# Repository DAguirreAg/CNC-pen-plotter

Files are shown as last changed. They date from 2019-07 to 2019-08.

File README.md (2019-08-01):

# CNC-pen-plotter
A multi axes (XY) CNC pen plotter machine.

<p align="middle">
  Drawing with the CNC machine

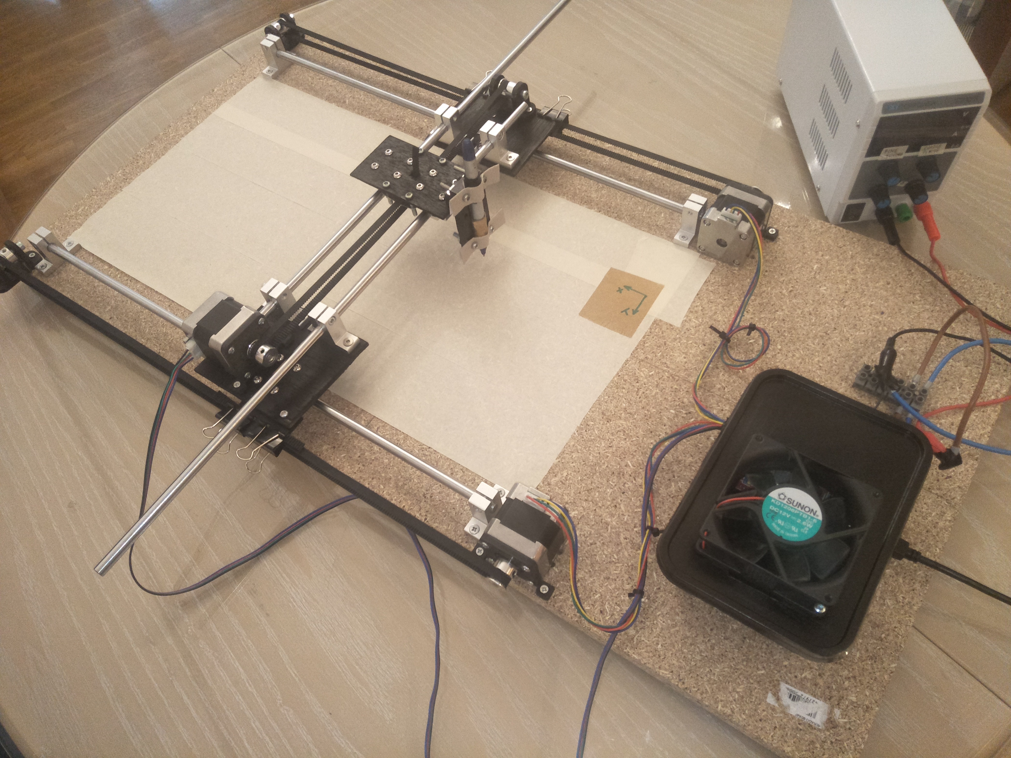
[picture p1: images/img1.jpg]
Complete view of the CNC assembly
  
</p>

## 1. Introduction
The following repository holds the code, schematics and hardware needed to build a simple two linear axes plotter controlled with an Arduino and a CNC shield. 

The X axis is controlled by **two Nema 17 stepper motors** and the Y axis is controlled by **another Nema 17 stepper motor**.

The commands are sent via the “Universal GCode sender” and the GCode can be generated using any slicer/CAM software (Inkscape, Fusion360,...).

### 2. Preparation
### 2.1. Hardware
The assembly process is quite straightforward:

1. Assembly the pulleys and pulley holders (3 in total).
2. Assembly the pulleys, the motors and the motor holders (3 in total).
3. Assembly the X shafts and the X shaft holders (2 in total).
4. Assembly the movable left side base.

<p align="middle">
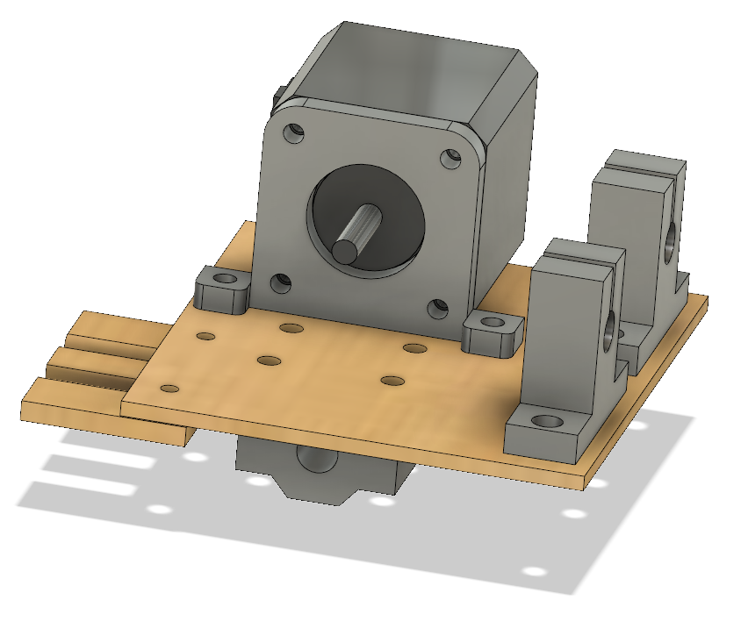
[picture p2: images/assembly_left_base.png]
Assembly of the movable left base
  
</p>

5. Assembly the movable right side base.

<p align="middle">
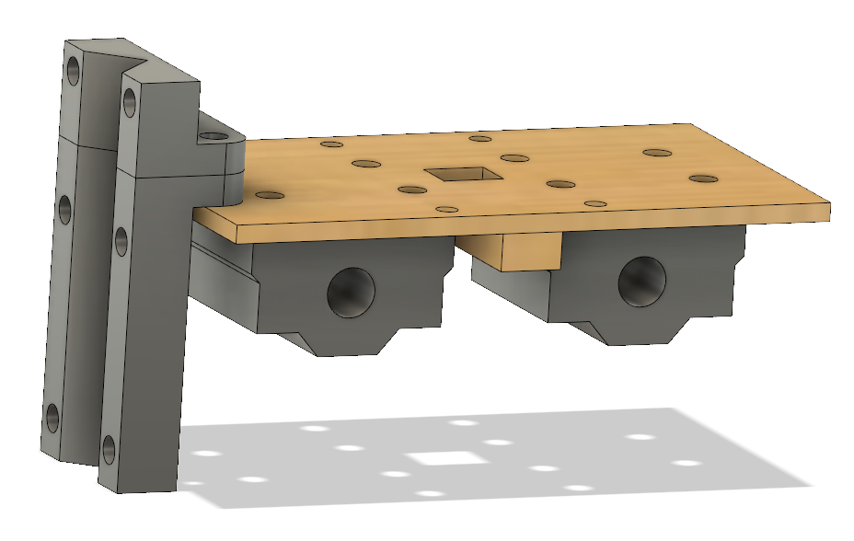
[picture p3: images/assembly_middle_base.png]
Assembly of the movable middle base
  
</p>

6. Assembly the movable middle base.

<p align="middle">
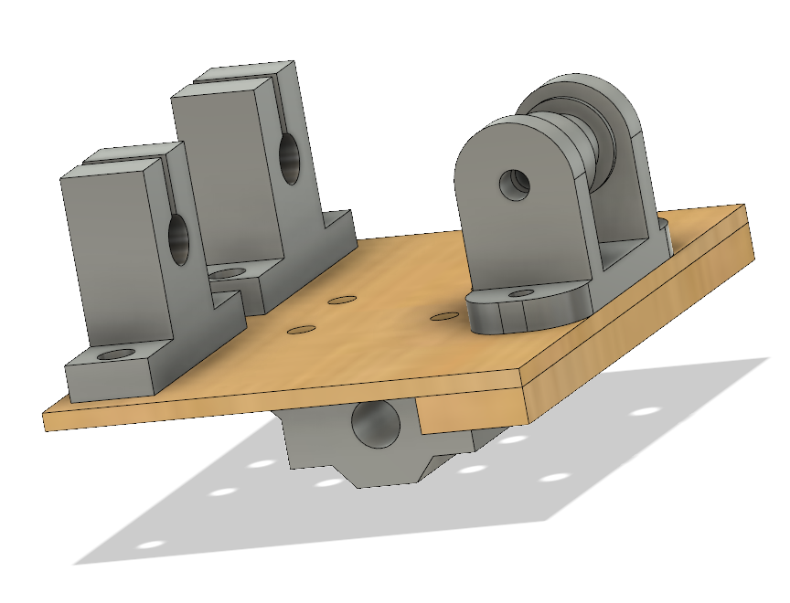
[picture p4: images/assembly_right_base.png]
Assembly of the movable right base
  
</p>

7. Assembly all the bases and shafts accordingly.

<p align="middle">
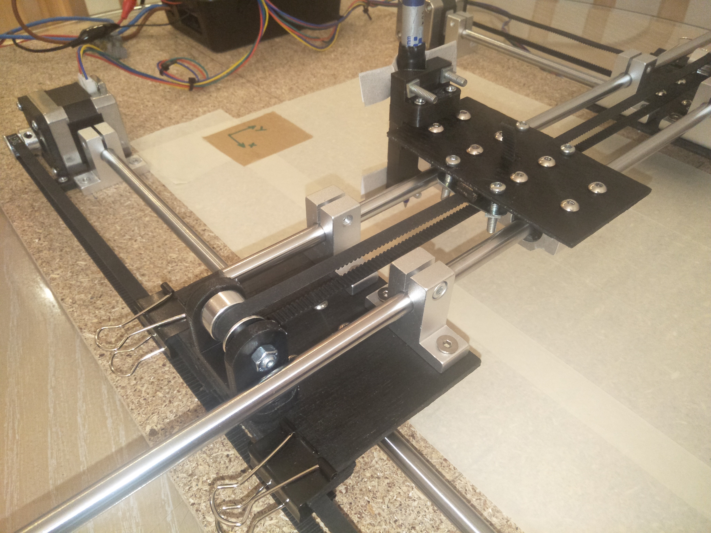
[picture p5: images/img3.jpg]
Complete assembly photo 1
  

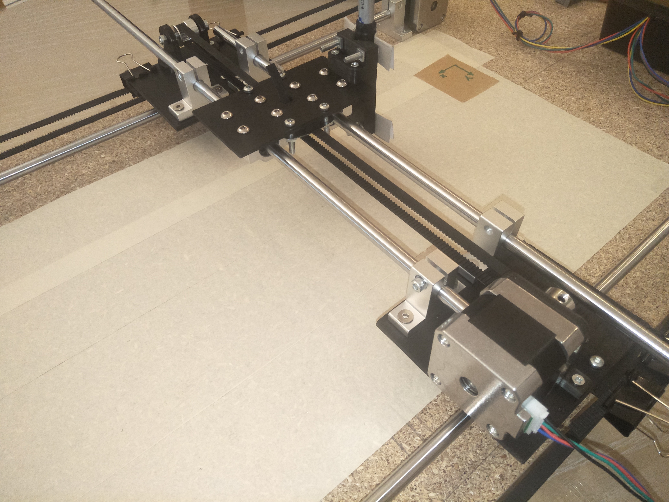
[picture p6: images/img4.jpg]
Complete assembly photo 2
  
  
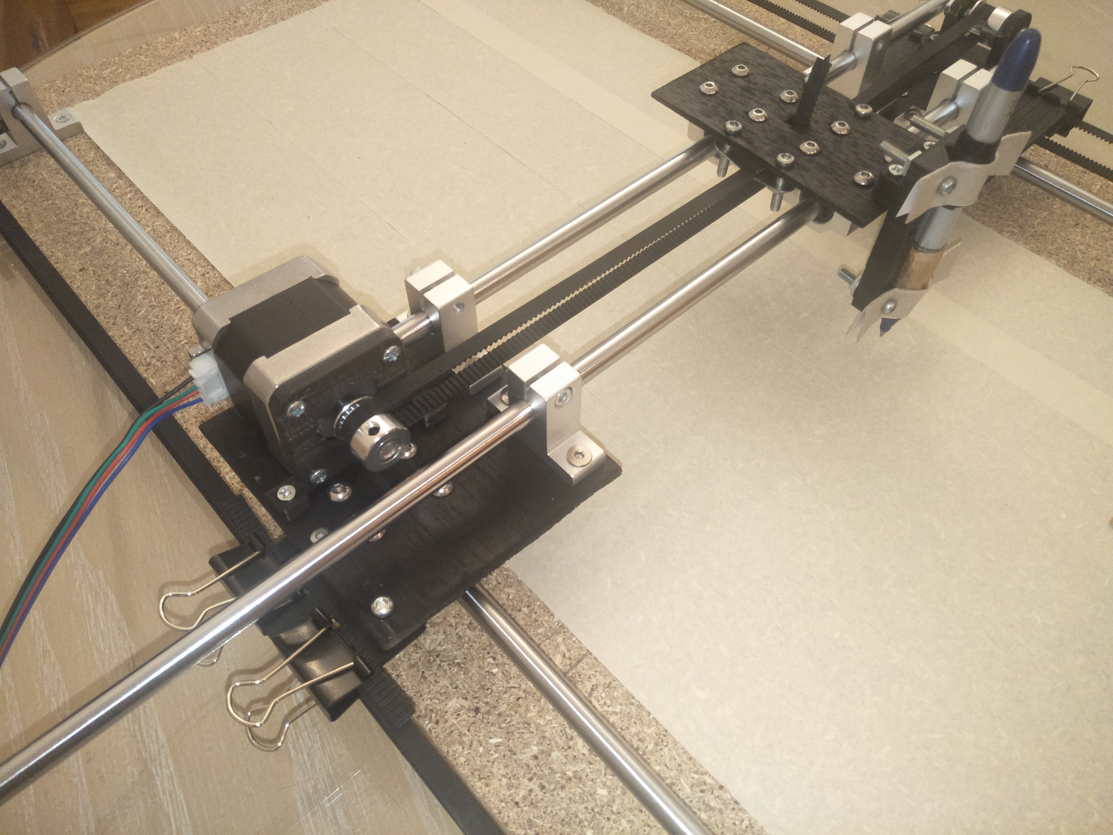
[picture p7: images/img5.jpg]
Complete assembly photo 3
  
</p>

8. Place the belts and make sure to tighten them up.
9. **Manually move the X and Y bases to check for uneven movements or noises**. Try loosing/tightening the screws and adjusting the different elements to make the movements as smooth as possible.

### 2.2. Electronics
Before proceeding with the electronics, I really recommend checking that all the components work properly. Pay special attention to **A4988** modules, as they **need to be tuned** before being used. Find a nice tutorial about tuning them [here](https://howtomechatronics.com/tutorials/arduino/how-to-control-stepper-motor-with-a4988-driver-and-arduino/).

After ensuring that all the components work properly follow next diagram to setup your electronics. Don't forget to **connect the X.STEPS/DIR pins** so the commands in the A axis are the same as the ones in the X axis (remember that the X direction is controlled by two motors!).

<p align="middle">
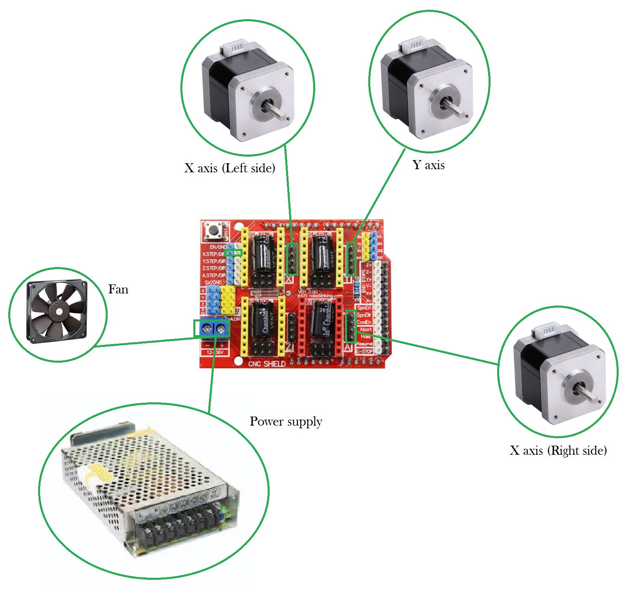
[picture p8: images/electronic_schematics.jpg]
Schematics for electronics assembly
  
</p>

### 2.3. Software
Install the GRBL into your Arduino. Find [here](https://arduinoboardproject.com/en/how-to-install-grbl-on-arduino-uno-with-the-arduino-ide-software/) some useful instructions on how to do this.

* Download and install [Universal Gcode Sender](https://winder.github.io/ugs_website/) for sending Gcode commands to the Arduino.
* Open Universal Gcode Sender and connect to the Arduino.

## 3. Setting up
Before drawing anything, we will need to check that everything is working correctly. In order to do that, please follow next steps:

1. Disconnect all the belts.
2. Test each motor’s rotation direction by sending the G0 X0 or G0 Y0 command. Change the wiring (WITHOUT power!) if needed to make sure the motors work as intended.
3. Place the belts once more and make sure to tighten them up.
4. Repeat the 2 step to make sure all the components work properly with the belts installed.
5. **If microstepping was enabled**, you will need to **adjust the step/mm relation** of each axis. This is a straighforward process, so follow [this](https://diymachining.com/grbl-steps-per-mm/). 
6. Congratulations!!!! You are ready to start drawing!!!

## 4. Drawing
Now that everything is ready, it is time to have some fun:

1. Generate a Gcode from any software you like (For beginners, you can start with Inkscape).
2. Open "Universal Gcode Sender" and connect to your arduino.
3. Open the Gcode you just created.
4. Press RUN and see the machine do its magic!!!!!

## 5. Requirements
### 5.1. Software
You should install/have the following software in order to control your CNC machine:

* [Universal Gcode Sender](https://winder.github.io/ugs_website/)
* [Arduino IDE](https://www.arduino.cc/en/main/software)
* [Inkscape](https://inkscape.org/)*
* [StippleGen](https://www.evilmadscientist.com/2012/stipplegen2/)*

*(Not necessary but recommended)

### 5.2. Components
In order to construct this project, you will need the following components:

* Microcontroller: Arduino UNO
* CNC shield: CNC shield V3.0
* Stepper motor driver: A4988
* Power supply: Voltage: 12V Amperage: 5A
* Pulley: Geared pulleys: 5mm, 20 teeth
* Transmission belt: GT2, 5mm
* Linear bearings: 8mm
* Shafts: 8mm, 500mm (2 pcs) and 250mm (2 pcs)
* Shaft holders: 8mm
* Fan: 12V

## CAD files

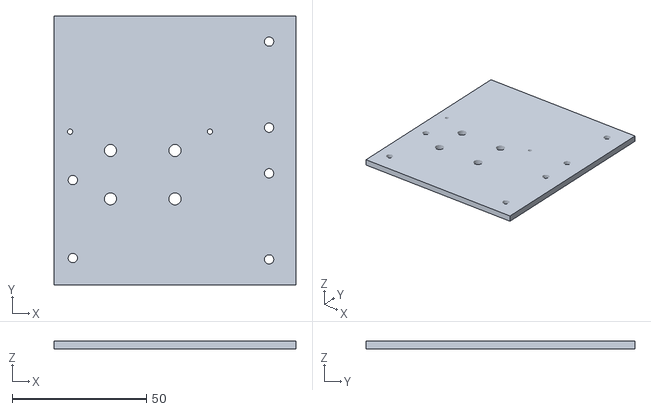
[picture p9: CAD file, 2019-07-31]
STL files/Base_X_left.stl
90.0 x 100.0 x 3.00

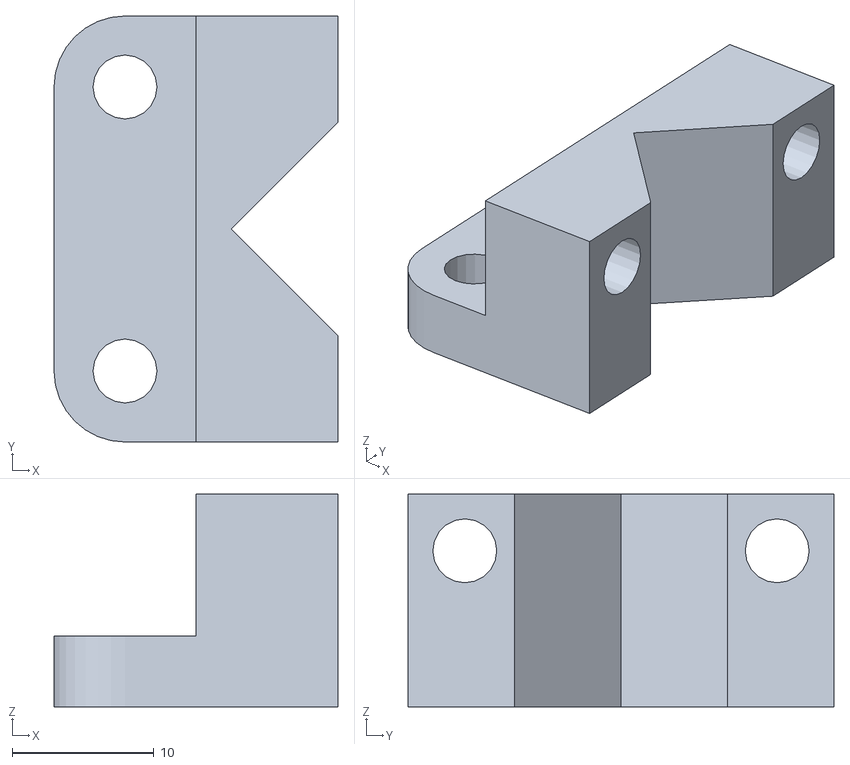
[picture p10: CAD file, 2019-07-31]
STL files/Pen_holder_upper_part.stl
20.0 x 30.0 x 15.0

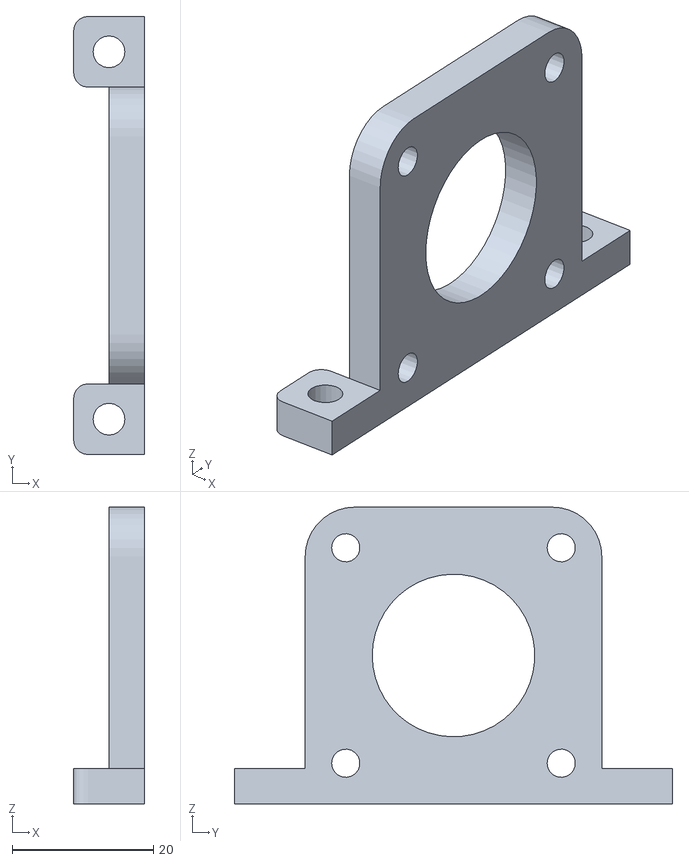
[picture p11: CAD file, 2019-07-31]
STL files/Motor_holder.stl
10.0 x 62.0 x 42.0

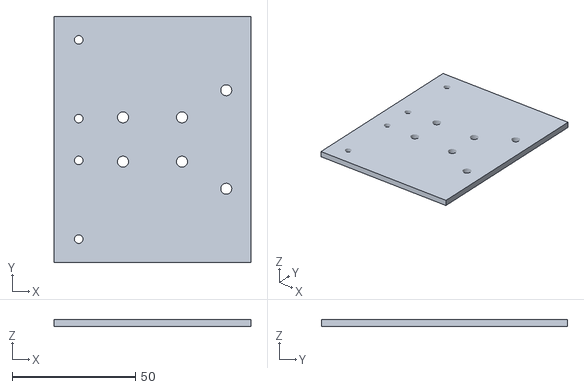
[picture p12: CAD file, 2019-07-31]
STL files/Base_X_right.stl
80.0 x 100.0 x 3.00

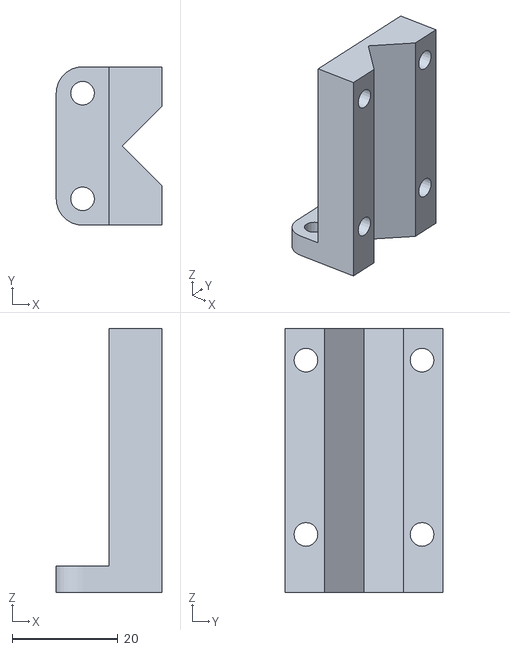
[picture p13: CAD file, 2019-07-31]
STL files/Pen_holder_lower_part.stl
20.0 x 30.0 x 50.0

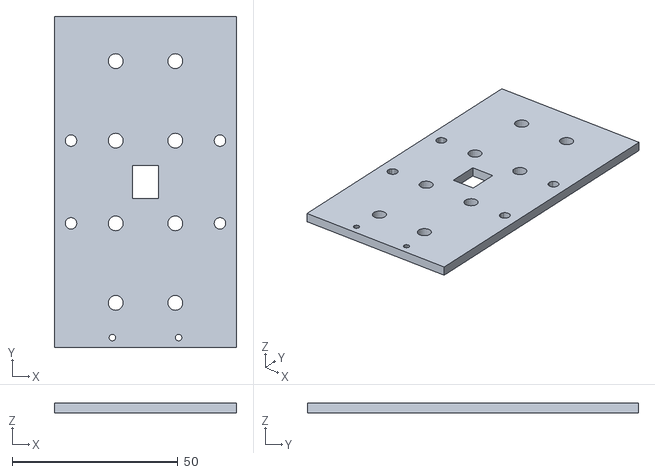
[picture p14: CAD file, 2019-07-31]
STL files/Base_Y.stl
55.0 x 100.0 x 3.00

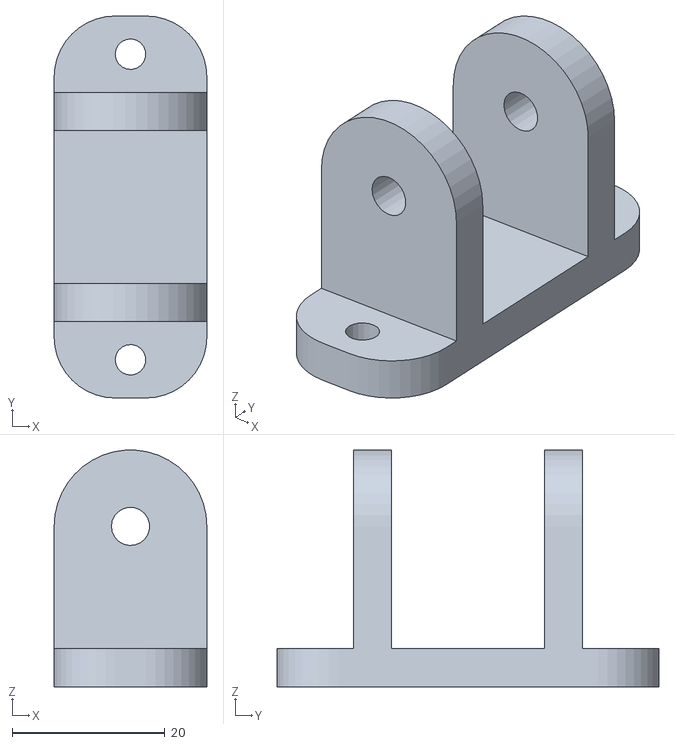
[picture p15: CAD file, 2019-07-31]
STL files/Pulley_holder.stl
20.0 x 50.0 x 31.0

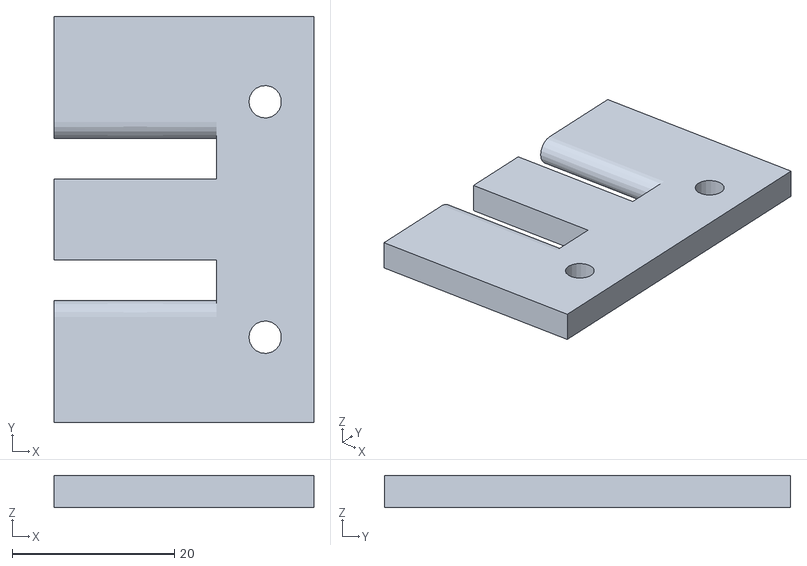
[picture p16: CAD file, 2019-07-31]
STL files/Clamp_X.stl
32.0 x 50.0 x 4.00

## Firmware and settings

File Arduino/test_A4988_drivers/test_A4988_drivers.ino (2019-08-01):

/*     Code for testing A4988 driver controlled stepper motors
 *      
 *  by Daniel Aguirre
 *  
 */
 
// defines pins numbers
const int stepPin = 3; 
const int dirPin = 4;  
const int buttonPin = 5; 
 
void setup() {
  // Set the pins
  pinMode(stepPin,OUTPUT); 
  pinMode(dirPin,OUTPUT);

  pinMode(buttonPin,INPUT);
  
}
void loop() {

  // Check if button was pressed
  if (digitalRead() == true){
    digitalWrite(dirPin,HIGH); 
    for(int x = 0; x < 200; x++) {
      digitalWrite(stepPin,HIGH); 
      delayMicroseconds(500); 
      digitalWrite(stepPin,LOW); 
      delayMicroseconds(500); 
    }
    
    delay(1000); 
    
    digitalWrite(dirPin,LOW); 
    for(int x = 0; x < 200; x++) {
      digitalWrite(stepPin,HIGH);
      delayMicroseconds(500);
      digitalWrite(stepPin,LOW);
      delayMicroseconds(500);
    }
    
    delay(1000);
  }
}
